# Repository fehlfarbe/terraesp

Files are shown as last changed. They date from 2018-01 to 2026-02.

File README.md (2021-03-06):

# ESP32 terrarium controller

With this project you can control your terrarium's temperature, light, sprinkler and so on via webinterface.

## Features

* Reads different Sensors for temperature and humidity (DHT22, SHT3x, DS1820, ...) and analog sensors to measure soil moisture etc.
* Timers for day/night light switch
* Actions if threshold for a sensor is reached e.g. to start sprinkler for 10s if humidity is under threshold
* Webinterface:
  * 24h log of temperature and humidity, actions etc.
  * control for buttons/actors and sliders for PWM pins
  * change config
* OTA update via WiFi

## Webinterface

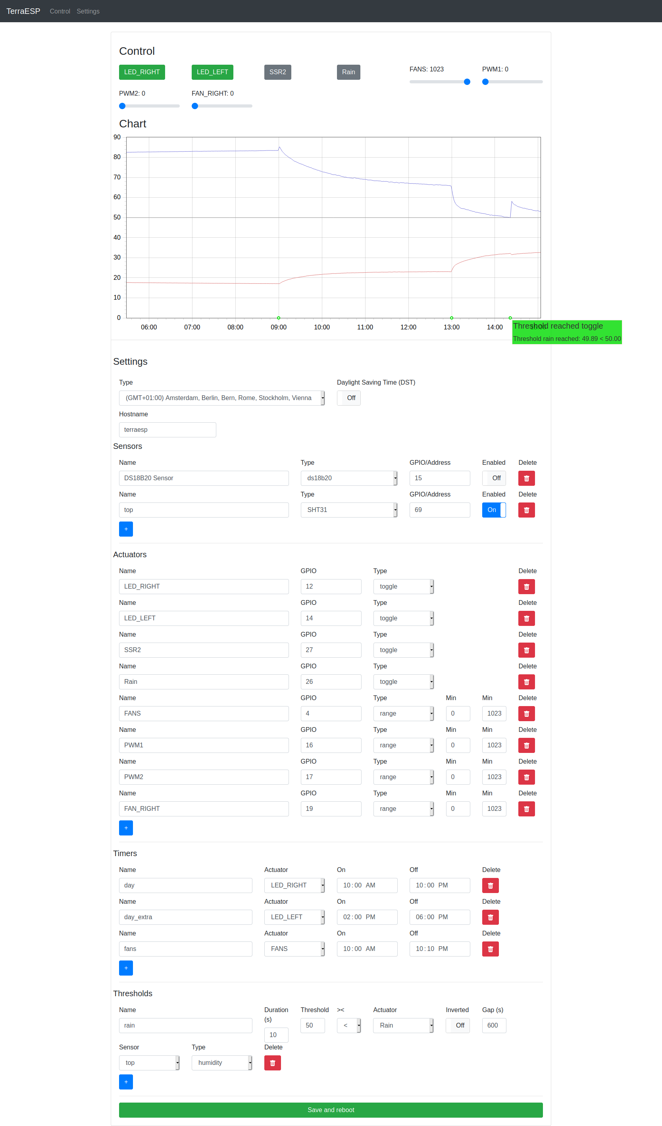
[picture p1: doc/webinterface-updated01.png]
webinterface Screenshot of webinterface


The webinterface has interactive controls to toggle relays or set PWM values to set the brightness of LEDs or fan speed.

A chart shows the measured temperatures (red) and humidity (blue) of your configured sensors and events (green) like time on, off and so on.

You can add sensors, actuators (relay, pwm), timers and thresholds in the 'settings' section.

## Parts needed

* ESP32 dev board
* DHT22 / SHT31 / analog temperature and humidity sensor
* Relay or SSR board to control lights/pump
* MOSFET board to control LED brightness, fan speed etc. via PWM
* WiFi connection for time sync

The device creates an access point on first start. Then you can configure your WiFi and pin settings.

## Caution

The WiFi password is saved without encryption on the device. Also OTA-update has default password "admin" at the moment. Change it if you want to secure your device for unauthorized updates.

> **Make the webinterface accessible from the internet is a very bad idea! Please use a VPN or something else to prevent a flooded terrarium ;-)**

## Installation

* Download / Clone this repository
* Install PlatformIO: <https://docs.platformio.org/en/latest/ide/pioide.html>
* Open this project in PlatformIO
* Connect your ESP32 via USB cable and upload sketch and [filesystem](https://docs.platformio.org/en/latest/platforms/espressif32.html#uploading-files-to-file-system-spiffs)
  * Run task -> Upload file system image
  * or run `pio run -t uploadfs`
  * Uploading filesystem will overwrite your settings!
* Reboot ESP32, it will create an AccessPoint with name ESP_xxxx
* Connect to the AP and open <http://192.168.4.1> in Browser
* Connect to your WiFi network
* Setup pins, sensor and so on in the webinterface

## Problems

* If PlatformIO can't find the libraries, switch to the cloned directory, open a terminal and type `pio lib install`. The command should download all necessary libraries.
* Windows users: if you get errors like `error: 'timeinfo' has incomplete type` just delete the `Time.h` header in `.pio/libdeps/{ota,usb}/Time` after installing the libs. The bug happens only on Windows because it's not case-sensitive and mixes the `time.h` header with `Time.h` of TimeLib library.

## PCB

Prototype PCB with several new features:

* 12V supply voltage for board and PWM/switches
* Directly soldered ESP32 with 12V -> 5V -> 3V3 converter
* 4x SSR to switch 230V AC with one 230V AC input and 3-4x outputs (is this safe??)
* 4x MOSFETs for PWM with supply voltage (to set the brightness of a 12V LED strip or control the speed of a fan)
* Connect multiple sensors/displays/whatever via i2c bus
* Connect analog sensors

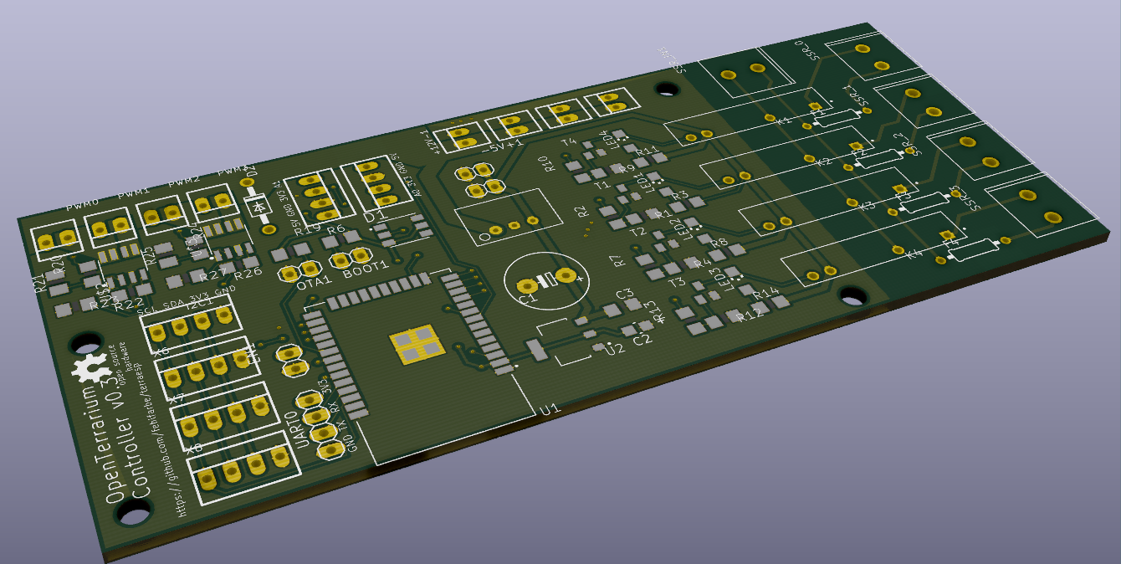
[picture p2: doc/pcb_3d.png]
PCB


## ToDo

* [ ] webinterface with authorization
* [ ] better instructions
* [ ] import/export config
* [x] The current hardware setup is a mess  with many jumper cables and so on. So I want to create PCB with relays/SSR, MOSFETS, power supply
* [ ] PID controller for heater/humidifier?
* [ ] PCB: switch from EAGLE to KiCAD (in progress...)
* [ ] PCB: replace the expensive 12V -> 5V step down (in progress...)

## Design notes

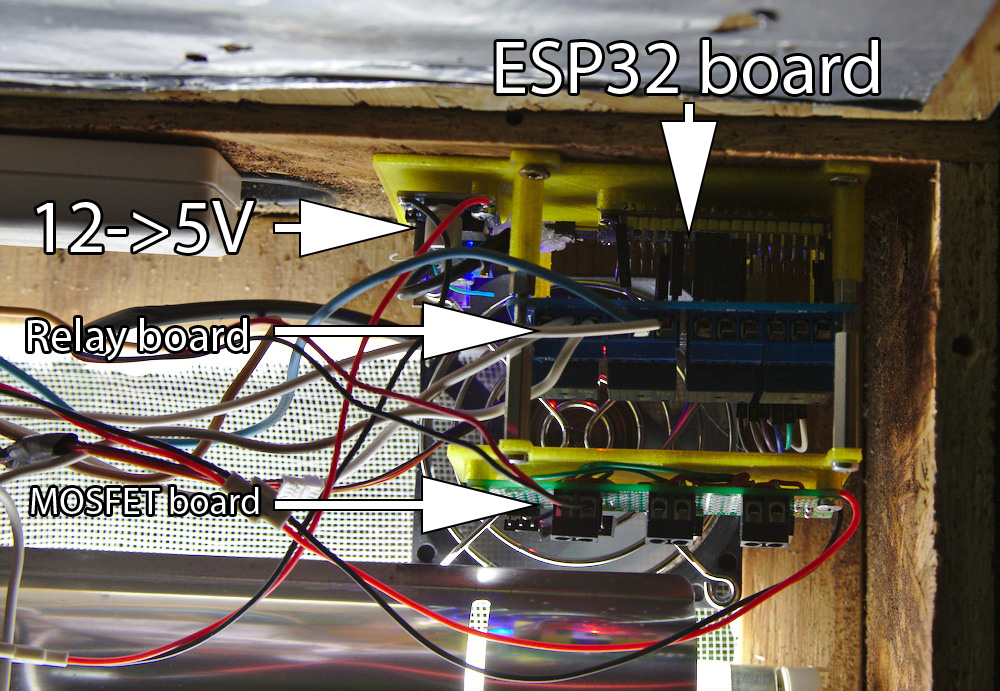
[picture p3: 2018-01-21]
doc/terrarium03.jpg

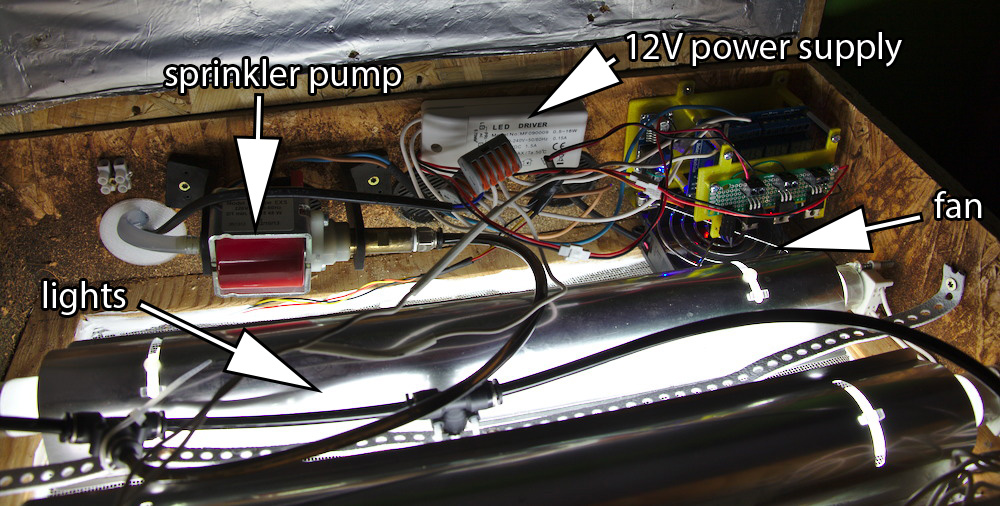
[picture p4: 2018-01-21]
doc/terrarium02.jpg

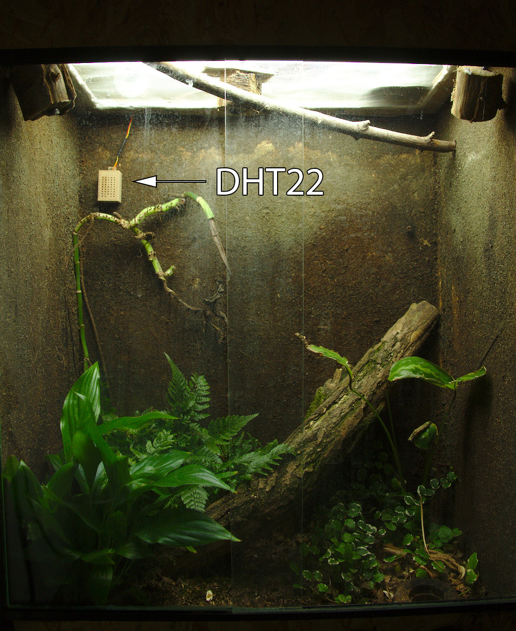
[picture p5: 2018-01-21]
doc/terrarium01.jpg

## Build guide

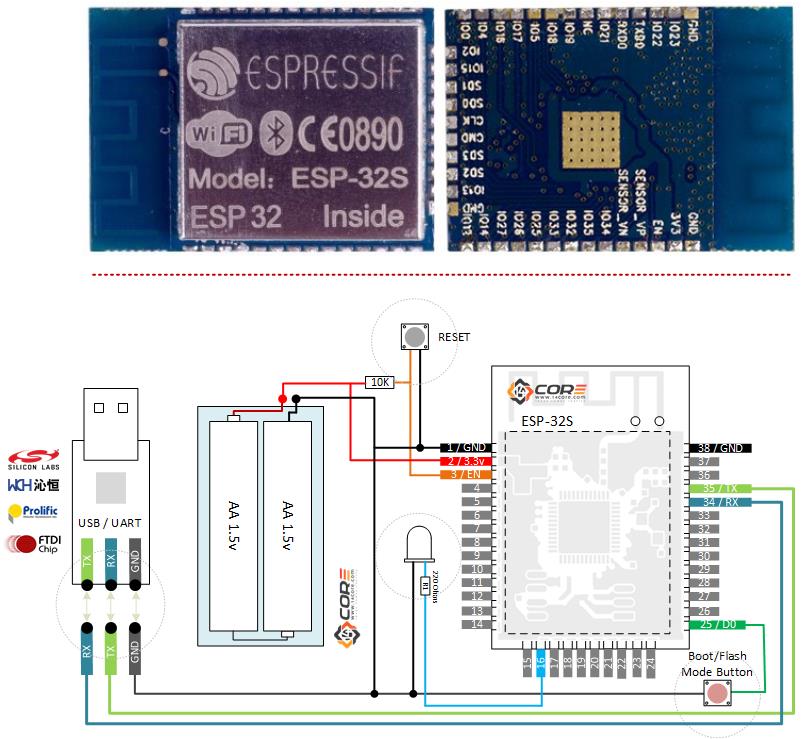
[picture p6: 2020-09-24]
doc/ESP32-Flash-USB-UART-Wiring-Guide-diagram.jpg

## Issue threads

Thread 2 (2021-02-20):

multiple time errors when compiling

jonathoncain, 2021-02-20:
I'm getting multiple time errors when compiling. specifically to deal with time.
[errors.txt](https://github.com/fehlfarbe/terraesp/files/6014123/errors.txt)

fehlfarbe, 2021-02-20:
Hi!
Did you try the master branch? I updated many things in [version2](https://github.com/fehlfarbe/terraesp/tree/version2 ) branch.

jonathoncain, 2021-02-20:
Yes I tried it first and was getting errors when compiling as well. I can
send the errors from that as well when I get home. It was right at the
beginning of the compiling. It was dealing with the feature/stage said it
wasnt in the upper stream or something like that.

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

jonathoncain, 2021-02-20:
I wanted to clarify my earlier response. Version2 is the one I was having the errors on. I uploaded a copy of the terminal output.

fehlfarbe, 2021-02-21:
Could be related to this problem: https://community.platformio.org/t/build-error-if-time-library-is-installed/450/6

I'm working on Linux so I can't really test it but I fixed some includes and I hope it will compile now.

jonathoncain, 2021-02-21:
its still failing with fewer errors.
[errors2.txt](https://github.com/fehlfarbe/terraesp/files/6017058/errors2.txt)

fehlfarbe, 2021-02-23:
I updated some imports and added a note for Windows users:

> Windows users: if you get errors like `error: 'timeinfo' has incomplete type` just delete the `Time.h` header in `.pio/libdeps/{ota,usb}/Time`. The bug happens only on Windows because it's not case-sensitive and mixes the `time.h` header with `Time.h` of TimeLib library.

It's a problem of the TimeLib dependency and the `Time.h` header will be removed in the future. After deleting `Time.h` it compiles on Windows.

jonathoncain, 2021-02-26:
The code is compiling without issue now. However it will not upload it says to specify upload port which I tried to add to the .ini file and have had no luck. It's like it doesn't recognize the board. If I create a new project and select the doit board version it uploads the blink sketch just fine so I don't know what the issue is

fehlfarbe, 2021-03-04:
Hey sorry for my late response. Did you select the USB environment in platformio?

You can also delete the OTA environment if you don't use OTA.:
```
[env:ota]
build_flags = -D RELEASE
upload_protocol = espota
upload_port = terraesp.local
upload_flags =
    --auth=admin
```

jonathoncain, 2021-03-06:
i figured it out it compiles and uploads. but when using the pio run -t uploadfs i get and error in the terminal windows that opens. i have attached the errors.
[error.txt](https://github.com/fehlfarbe/terraesp/files/6094764/error.txt)

fehlfarbe, 2021-03-06:
I added `mklittlefs.exe` to the project that should enable LittleFS build for Windows. Please pull and try again :)

jonathoncain, 2021-03-07:
thank you for all the help. its working now

fehlfarbe, 2021-03-07:
You're welcome! Feel free to open a new issue if you need more help.

Closed 2021-03-07.

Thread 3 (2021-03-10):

temp sensor not working

jonathoncain, 2021-03-10:
I have gotten it working and have it connected to the WIFI but I'm experiencing two issues.  the temp sensor isnt working i have tried a dht11 and dht22 (I noticed there isn't an option for the dht22 but i tried it on the 11 setting). I was using the pull-up resistor with the sensors. the other isue is its not geting the time from the internet it always starts at 00:00 when i connect it.

fehlfarbe, 2021-03-27:
Hey sorry for long response time. I have too much work at the moment.
I switched back to Adafruit DHT library and tried with AM2301 sensor which was working.

Time problem: can you ping `0.de.pool.ntp.org` and `1.de.pool.ntp.org` that's the NTP servers I'm using for time sync at the moment. Maybe I should add an option to set time via browser interface.

jonathoncain, 2021-03-29:
I'm not sure what is happening but once I upload the new version2 the esp never turns on the access point for me to connect to my home Wi-Fi. I uploaded the old version and it works so I'm assuming something is broken since the update. I also had a question is the master still different than version2 or are they the same now. should I just be using the master or version2. I have been using the master to upload the filesystem because it still fails on version2 then I switch to version to to upload the code.

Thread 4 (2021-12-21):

Problem Compiling

TomBoundless, 2021-12-21:
Sorry if this is not the correct place to post this, but I'm having issues around the DHT sensor.

In file included from src/sensors/dht_sensor.cpp:1:0:
src/sensors/dht_sensor.h:24:9: error: 'DHT' does not name a type
         DHT *sensor = nullptr;
         ^
src/sensors/dht_sensor.cpp: In constructor 'DHT11Sensor::DHT11Sensor(String, uint8_t, uint8_t)':
src/sensors/dht_sensor.cpp:7:5: error: 'sensor' was not declared in this scope
     sensor = new DHT(pin, type);
     ^
src/sensors/dht_sensor.cpp:7:18: error: expected type-specifier before 'DHT'
     sensor = new DHT(pin, type);
                  ^
src/sensors/dht_sensor.cpp: In member function 'bool DHT11Sensor::updateValues()':
src/sensors/dht_sensor.cpp:34:21: error: 'sensor' was not declared in this scope
     m_temperature = sensor->readTemperature();
                     ^
src/sensors/dht_sensor.cpp:95:1: warning: no return statement in function returning non-void [-Wreturn-type]
 }
 ^
*** [.pio\build\usb\src\sensors\dht_sensor.cpp.o] Error 1

I can't seem to figure out what the problem is. Running on platformio in VS Code.

fehlfarbe, 2021-12-21:
Does it work when you open a terminal in VSCode and install the libraries with `pio lib install`?

TomBoundless, 2021-12-21:
It doesn't unfortunately.

The annoying thing is I'm not even using the DHT sensor, planning on using an SHT

fehlfarbe, 2021-12-21:
Quick fix: I removed the include of dht_sensor in terrasesp.cpp and created a new branch: https://github.com/fehlfarbe/terraesp/tree/no-dht can you try it?

TomBoundless, 2021-12-21:
Thanks for your quick responses.

It's giving me the same error again.

fehlfarbe, 2021-12-21:
Maybe I found the initial bug: are you using Windows? There is a different/old `dht.h` in the `src` directory. Maybe Windows includes the old `dht.h` in `src` directory instead of the Adafruit `DHT.h` because it's case-insensitive. I removed the old `dht.h` in my latest commit on master branch.

TomBoundless, 2021-12-21:
I am using Windows.

That latest commit has solved the problem and it has now successfully compiled!

Thanks very much for your help, this will make a brilliant Christmas present for my girlfriend.

fehlfarbe, 2021-12-21:
Perfect! :smiley:
Just open a new issue if something else doesn't work.

TomBoundless, 2021-12-21:
Thanks very much!

Closed 2021-12-21.

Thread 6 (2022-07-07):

Compiling error

Eisbaeeer, 2022-07-07:
Platformio get an error by compiling the code.
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

src/Threshold.cpp:132:43: error: call of overloaded 'abs(long unsigned int)' is ambiguous

LuigiPapparotti, 2023-07-29:
Cast the argument to **abs()** to **int** or another suitable type:

`if(is_active && abs(((int)millis()-activated))/1000.0 > duration){`

Closed 2023-10-19.

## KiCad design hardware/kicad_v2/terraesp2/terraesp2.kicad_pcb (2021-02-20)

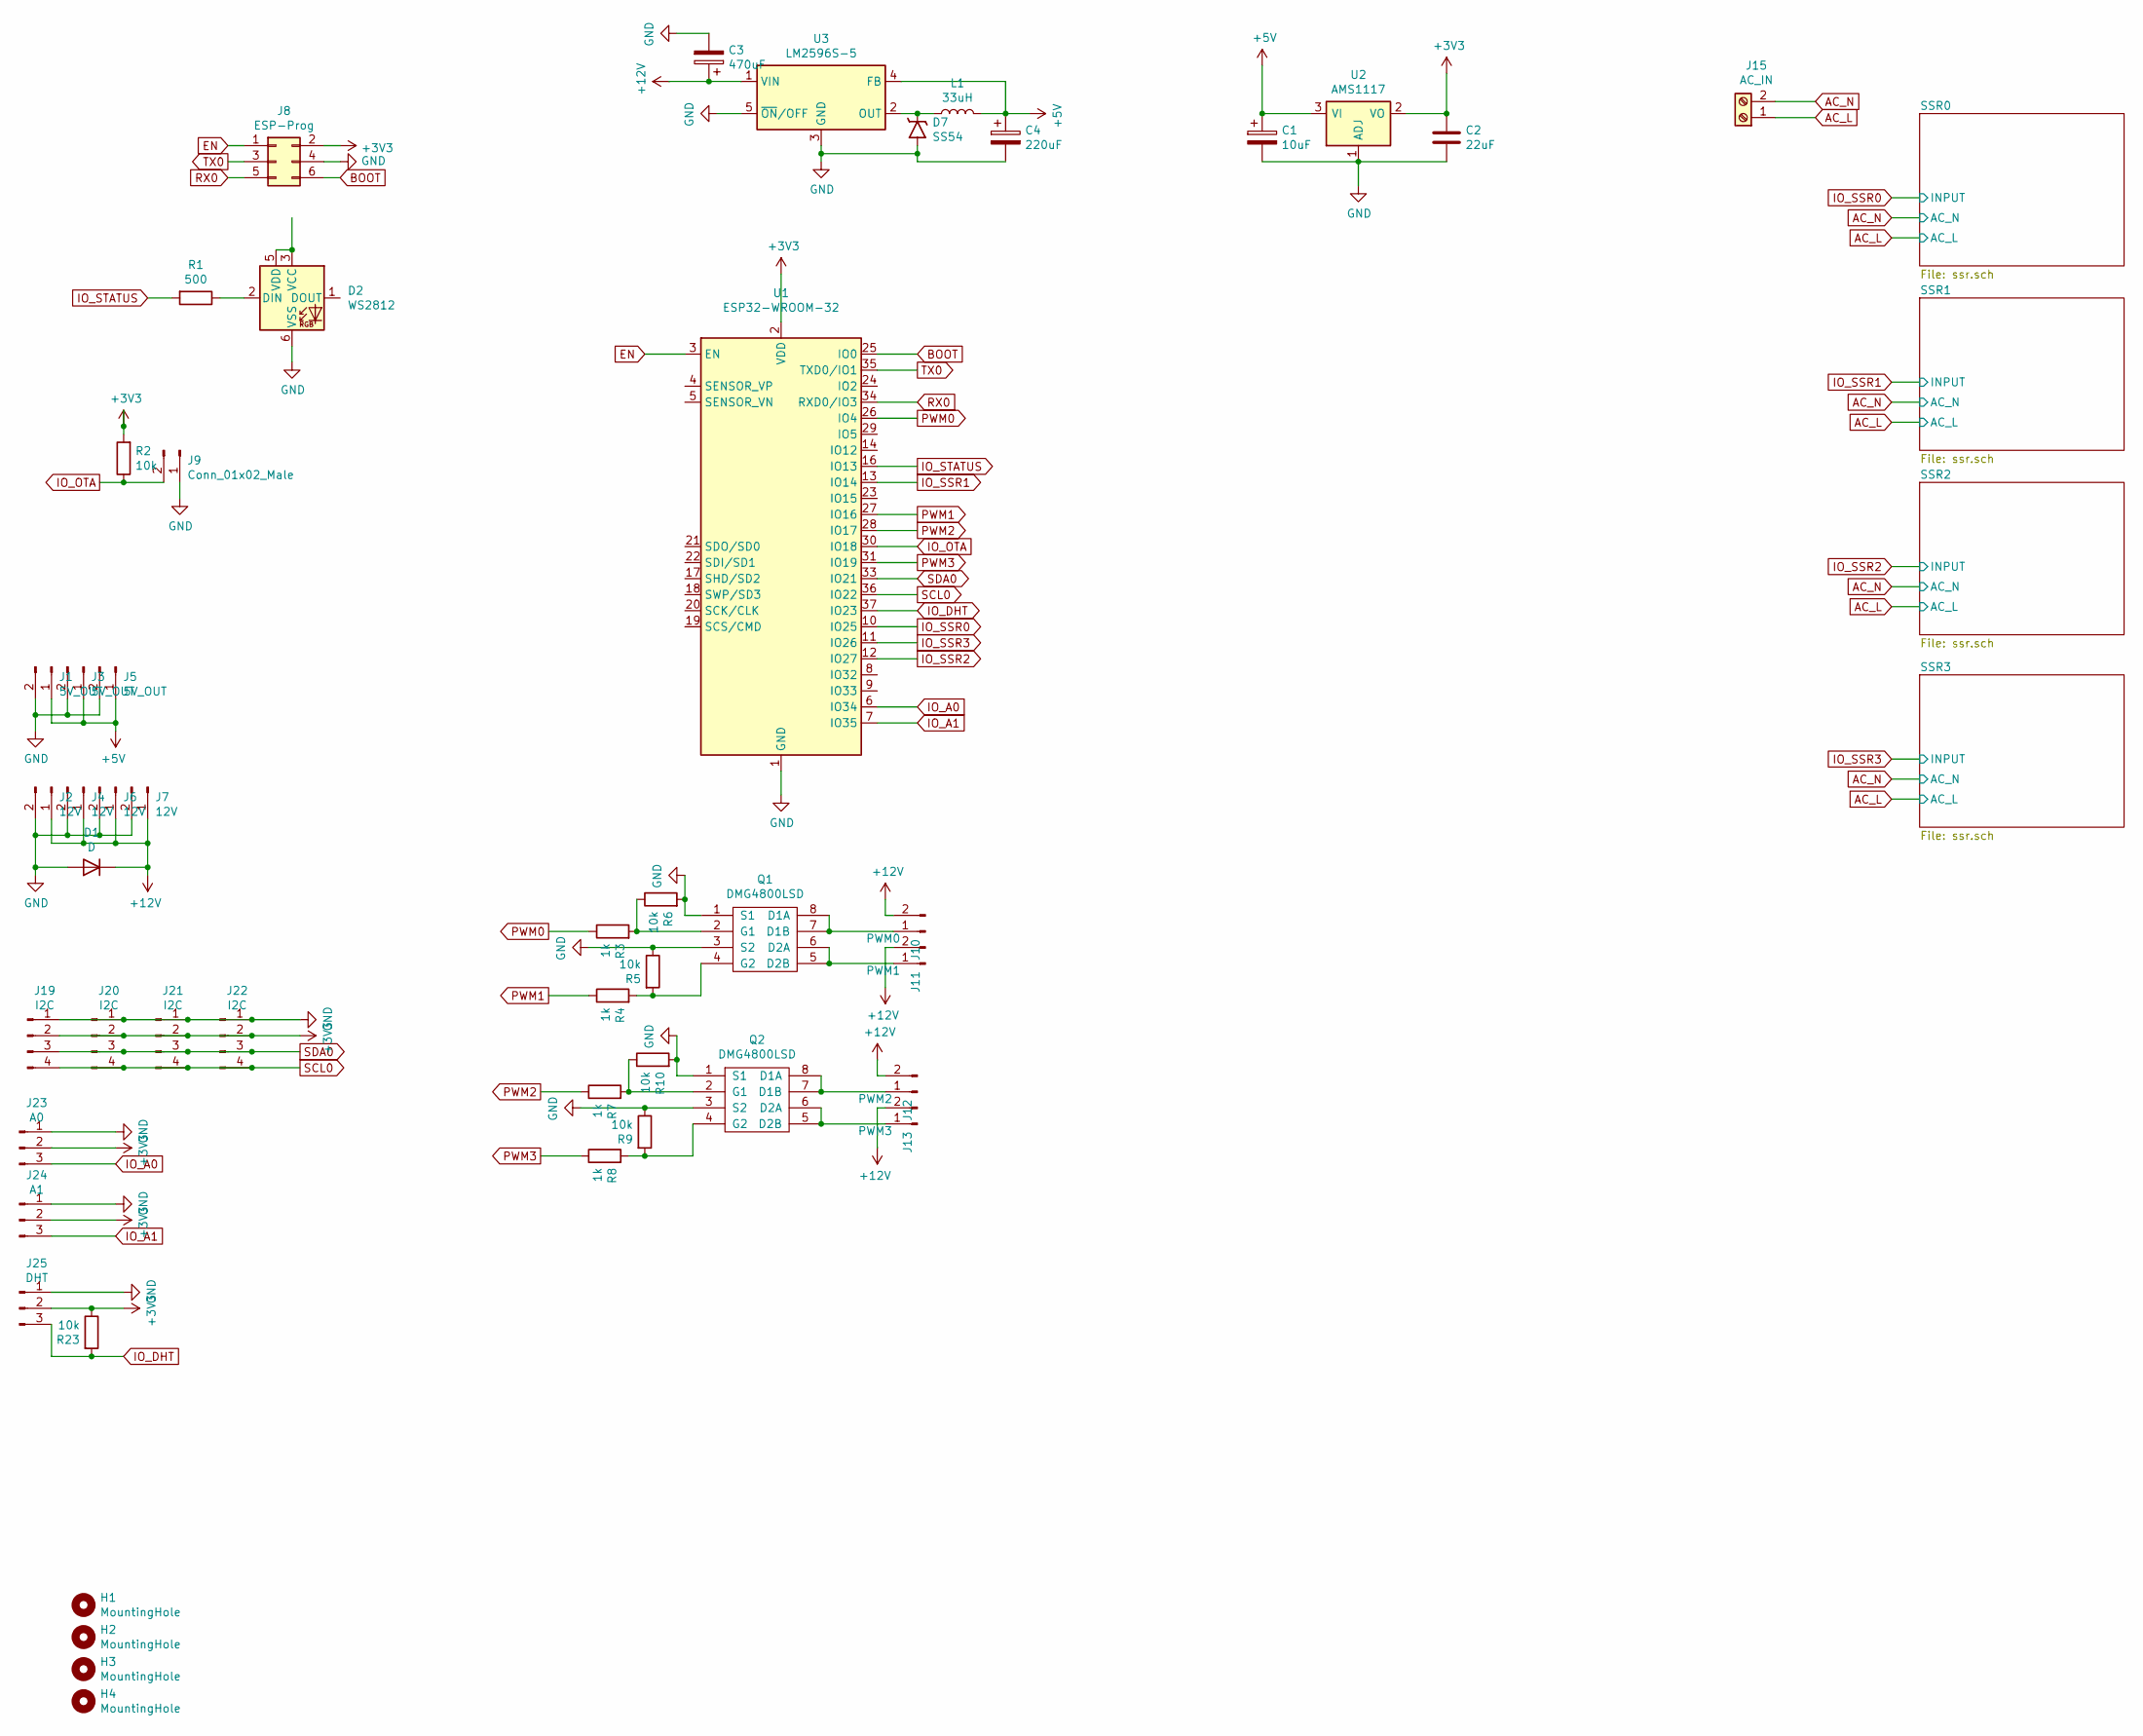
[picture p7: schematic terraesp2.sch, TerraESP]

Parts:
C1: 10uF; C_1206_3216Metric
C2: 22uF; CP_EIA-1608-08_AVX-J
C3: 470uF; CP_Elec_10x10.5
C4: 220uF; CP_Elec_6.3x5.8
D1: D; D_1206_3216Metric
D2: WS2812; LED_WS2812_PLCC6_5.0x5.0mm_P1.6mm
D7: SS54; DO-214AC
H1, H2, H3, H4: MountingHole; MountingHole_3.2mm_M3
J1, J3, J5: 5V_OUT; Molex_KK-254_AE-6410-02A_1x02_P2.54mm_Vertical
J2, J4, J6, J7: 12V; Molex_KK-254_AE-6410-02A_1x02_P2.54mm_Vertical
J8: ESP-Prog; IDC-Header_2x03_P2.54mm_Vertical
J9: Conn_01x02_Male; PinHeader_1x02_P2.54mm_Vertical
J10: PWM0; Molex_KK-254_AE-6410-02A_1x02_P2.54mm_Vertical
J11: PWM1; Molex_KK-254_AE-6410-02A_1x02_P2.54mm_Vertical
J12: PWM2; Molex_KK-254_AE-6410-02A_1x02_P2.54mm_Vertical
J13: PWM3; Molex_KK-254_AE-6410-02A_1x02_P2.54mm_Vertical
J15: AC_IN; TerminalBlock_Phoenix_MKDS-1,5-2_1x02_P5.00mm_Horizontal
J19, J20, J21, J22: I2C; Molex_KK-254_AE-6410-04A_1x04_P2.54mm_Vertical
J23: A0; Molex_KK-254_AE-6410-03A_1x03_P2.54mm_Vertical
J24: A1; Molex_KK-254_AE-6410-03A_1x03_P2.54mm_Vertical
J25: DHT; Molex_KK-254_AE-6410-03A_1x03_P2.54mm_Vertical
L1: 33uH; L_12x12mm_H8mm
Q1, Q2: DMG4800LSD; Diodes_Inc.-SO-8-03_2017-0-MFG
R1: 500; R_1206_3216Metric
R2, R5, R6, R9, R10, R23: 10k; R_1206_3216Metric
R3, R4, R7, R8: 1k; R_1206_3216Metric
U1: ESP32-WROOM-32
U2: AMS1117; SOT-223-3_TabPin2
U3: LM2596S-5; TO-263-5_TabPin3

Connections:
+3V3: C2.1, J8.2, J19.2, J20.2, J21.2, J22.2, J23.2, J24.2, J25.2, R2.2, R23.1, U1.2 (VDD), U2.2 (VO)
+5V: C1.1, C4.1, J1.1, J3.1, J5.1, L1.2, U2.3 (VI), U3.4 (FB); also elsewhere on the board
+12V: C3.1, D1.1 (K), J2.1, J4.1, J6.1, J7.1, J10.2, J11.2, J12.2, J13.2, U3.1 (VIN)
AC_L: J15.1; also elsewhere on the board
AC_N: J15.2; also elsewhere on the board
BOOT: J8.6, U1.25 (IO0)
EN: J8.1, U1.3 (EN)
GND: C1.2, C2.2, C3.2, C4.2, D1.2 (A), D2.6 (VSS), D7.A, J1.2, J2.2, J3.2, J4.2, J5.2, J6.2, J7.2, J8.4, J9.1, J19.1, J20.1, J21.1, J22.1, J23.1, J24.1, J25.1, Q1.1 (S1), Q1.3 (S2), Q2.1 (S1), Q2.3 (S2), R5.1, R6.2, R9.1, R10.2, U1.1 (GND), U1.15 (GND), U1.38 (GND), U1.39 (GND), U2.1 (ADJ), U3.3 (GND), U3.5 (~ON~/OFF); also elsewhere on the board
IO_A0: J23.3, U1.6 (IO34)
IO_A1: J24.3, U1.7 (IO35)
IO_DHT: J25.3, R23.2, U1.37 (IO23)
IO_OTA: J9.2, R2.1, U1.30 (IO18)
IO_SSR0: U1.10 (IO25); also elsewhere on the board
IO_SSR1: U1.13 (IO14); also elsewhere on the board
IO_SSR2: U1.12 (IO27); also elsewhere on the board
IO_SSR3: U1.11 (IO26); also elsewhere on the board
IO_STATUS: R1.2, U1.16 (IO13)
unnamed: D2.2 (DIN), R1.1
unnamed: D2.3 (VCC), D2.5 (VDD)
unnamed: D7.C, L1.1, U3.2 (OUT)
unnamed: J10.1, Q1.7 (D1B), Q1.8 (D1A)
unnamed: J11.1, Q1.5 (D2B), Q1.6 (D2A)
unnamed: J12.1, Q2.7 (D1B), Q2.8 (D1A)
unnamed: J13.1, Q2.5 (D2B), Q2.6 (D2A)
unnamed: Q1.2 (G1), R3.2, R6.1
unnamed: Q1.4 (G2), R4.2, R5.2
unnamed: Q2.2 (G1), R7.2, R10.1
unnamed: Q2.4 (G2), R8.2, R9.2
PWM0: R3.1, U1.26 (IO4)
PWM1: R4.1, U1.27 (IO16)
PWM2: R7.1, U1.28 (IO17)
PWM3: R8.1, U1.31 (IO19)
RX0: J8.5, U1.34 (RXD0/IO3)
SCL0: J19.4, J20.4, J21.4, J22.4, U1.36 (IO22)
SDA0: J19.3, J20.3, J21.3, J22.3, U1.33 (IO21)
TX0: J8.3, U1.35 (TXD0/IO1)

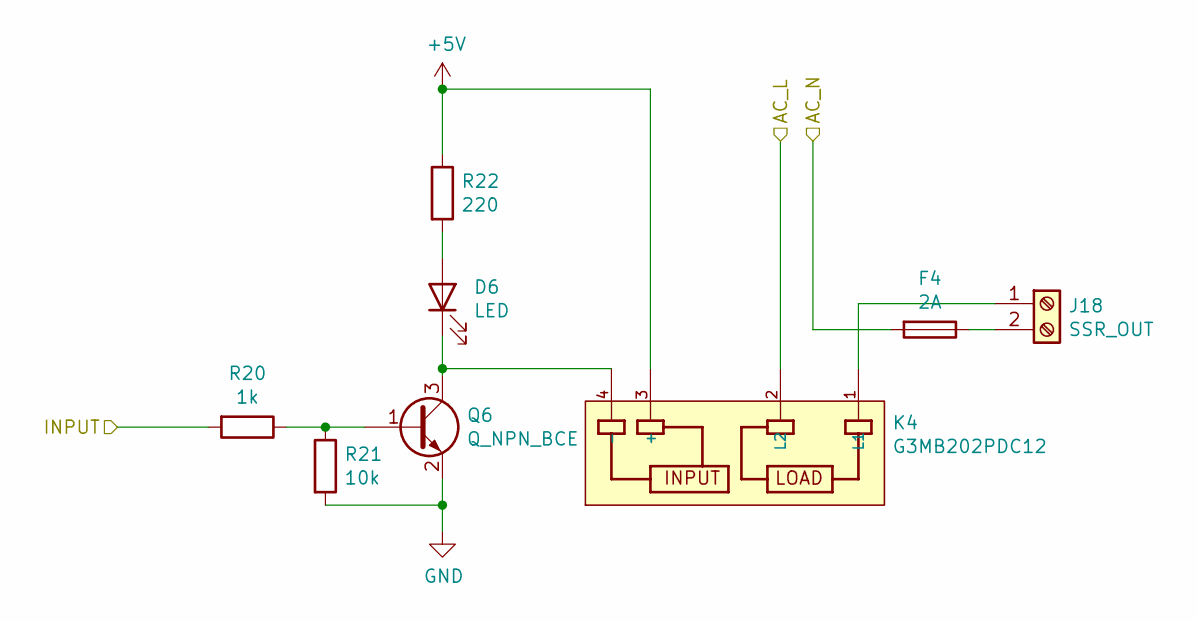
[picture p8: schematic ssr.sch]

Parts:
D3: LED; LED_1206_3216Metric
F1: 2A; ASI PTF-76 5x20mm Fuse Holder
J14: SSR_OUT; TerminalBlock_Phoenix_MKDS-1,5-2_1x02_P5.00mm_Horizontal
K1: G3MB202PDC12; RELAY_G3MB202PDC12; PARTREV N/A
Q3: Q_NPN_BCE; SOT-23
R11: 1k; R_1206_3216Metric
R12: 10k; R_1206_3216Metric
R13: 220; R_1206_3216Metric

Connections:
+5V: K1.3 (+), R13.1; also elsewhere on the board
AC_L: K1.2 (L2); also elsewhere on the board
AC_N: F1.2; also elsewhere on the board
GND: Q3.2 (E), R12.2; also elsewhere on the board
IO_SSR0: R11.2; also elsewhere on the board
unnamed: D3.1 (K), K1.4 (-), Q3.3 (C)
unnamed: D3.2 (A), R13.2
unnamed: F1.1, J14.2
unnamed: J14.1, K1.1 (L1)
unnamed: Q3.1 (B), R11.1, R12.1

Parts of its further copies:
D4, D5, D6: LED; LED_1206_3216Metric
F2, F3, F4: 2A; ASI PTF-76 5x20mm Fuse Holder
J16, J17, J18: SSR_OUT; TerminalBlock_Phoenix_MKDS-1,5-2_1x02_P5.00mm_Horizontal
K2, K3, K4: G3MB202PDC12; RELAY_G3MB202PDC12; PARTREV N/A
Q4, Q5, Q6: Q_NPN_BCE; SOT-23
R14, R17, R20: 1k; R_1206_3216Metric
R15, R18, R21: 10k; R_1206_3216Metric
R16, R19, R22: 220; R_1206_3216Metric

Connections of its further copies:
+5V: K2.3 (+), K3.3 (+), K4.3 (+), R16.1, R19.1, R22.1; also elsewhere on the board
AC_L: K2.2 (L2), K3.2 (L2), K4.2 (L2); also elsewhere on the board
AC_N: F2.2, F3.2, F4.2; also elsewhere on the board
GND: Q4.2 (E), Q5.2 (E), Q6.2 (E), R15.2, R18.2, R21.2; also elsewhere on the board
IO_SSR1: R14.2; also elsewhere on the board
IO_SSR2: R17.2; also elsewhere on the board
IO_SSR3: R20.2; also elsewhere on the board
unnamed: D4.1 (K), K2.4 (-), Q4.3 (C)
unnamed: D4.2 (A), R16.2
unnamed: D5.1 (K), K3.4 (-), Q5.3 (C)
unnamed: D5.2 (A), R19.2
unnamed: D6.1 (K), K4.4 (-), Q6.3 (C)
unnamed: D6.2 (A), R22.2
unnamed: F2.1, J16.2
unnamed: F3.1, J17.2
unnamed: F4.1, J18.2
unnamed: J16.1, K2.1 (L1)
unnamed: J17.1, K3.1 (L1)
unnamed: J18.1, K4.1 (L1)
unnamed: Q4.1 (B), R14.1, R15.1
unnamed: Q5.1 (B), R17.1, R18.1
unnamed: Q6.1 (B), R20.1, R21.1

Board: 2 copper layers, 81 parts (0 on the bottom side), 56 nets, no tracks yet.

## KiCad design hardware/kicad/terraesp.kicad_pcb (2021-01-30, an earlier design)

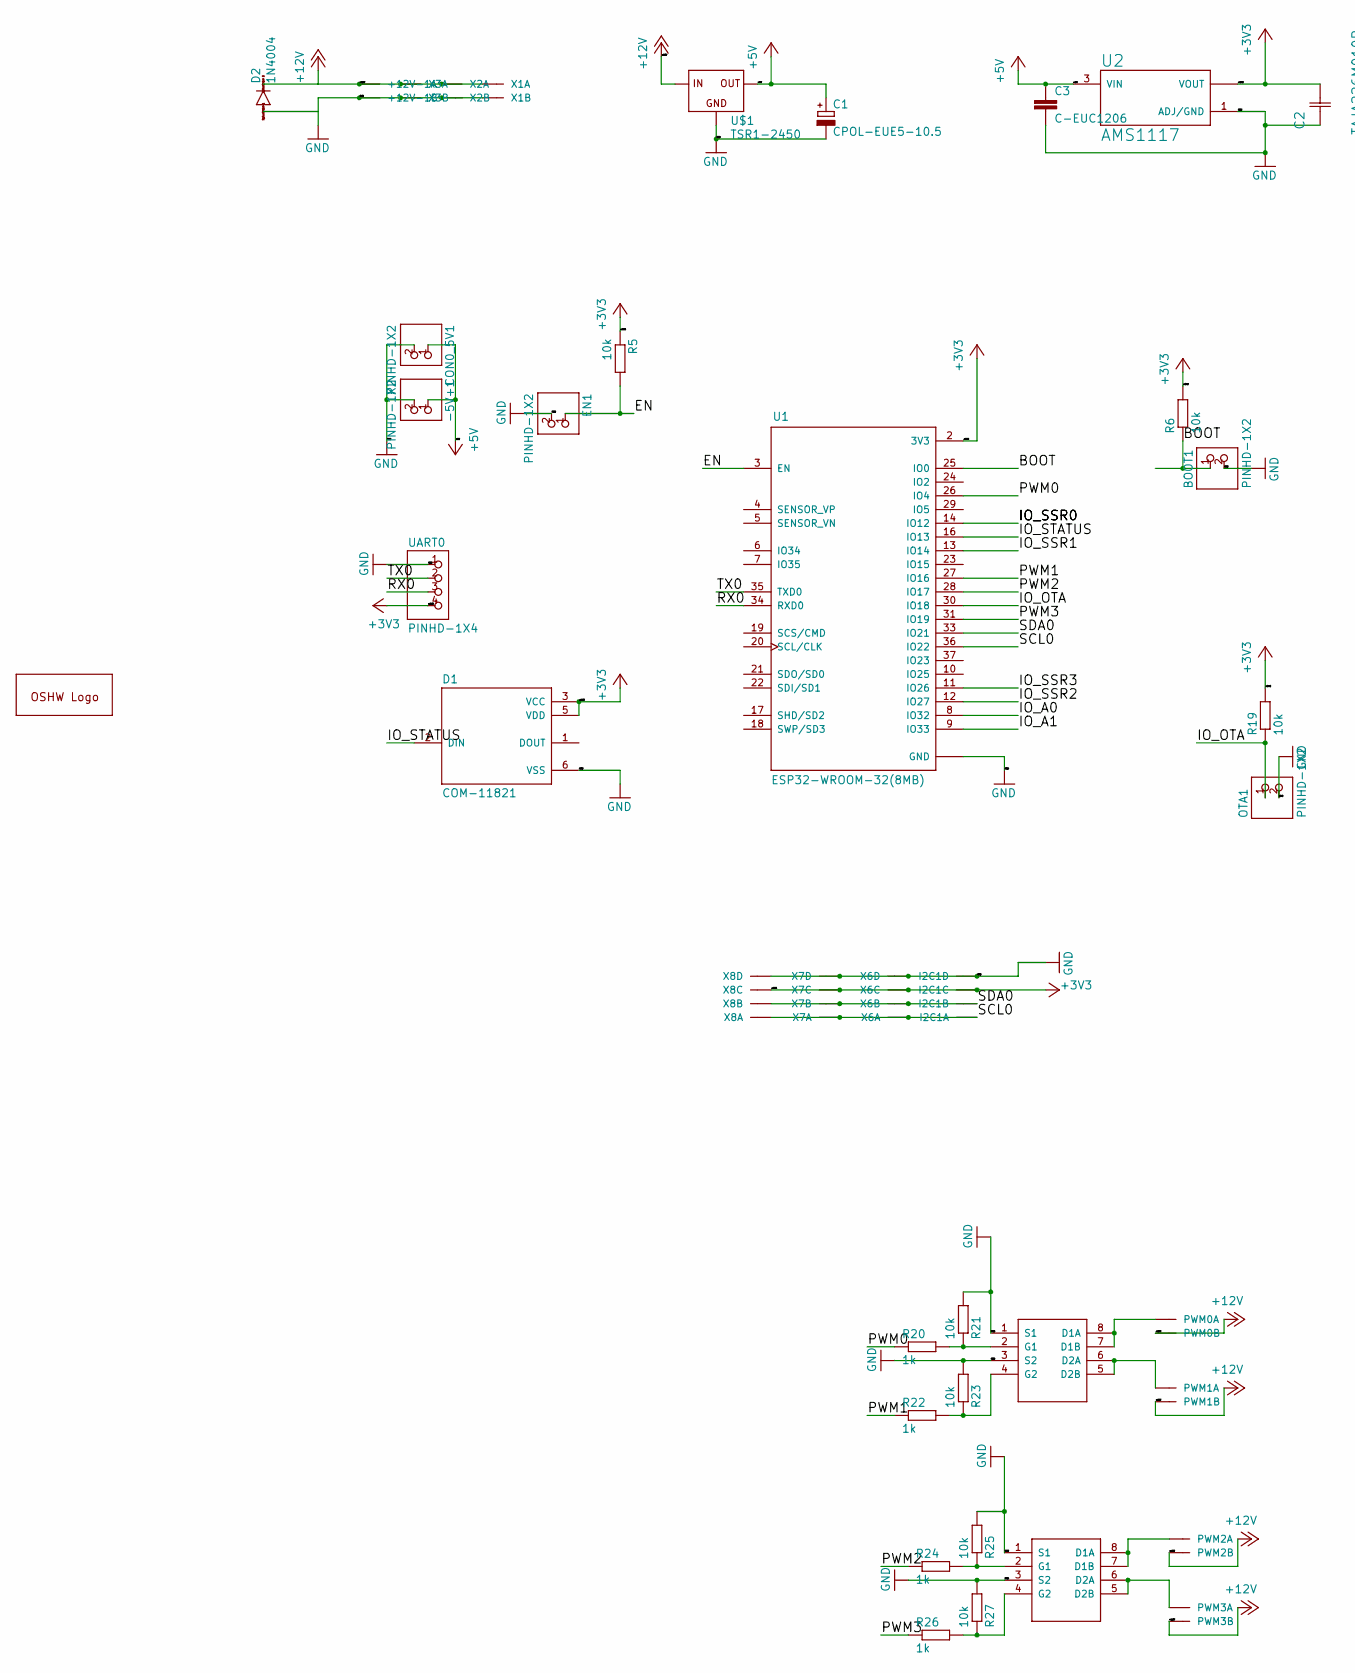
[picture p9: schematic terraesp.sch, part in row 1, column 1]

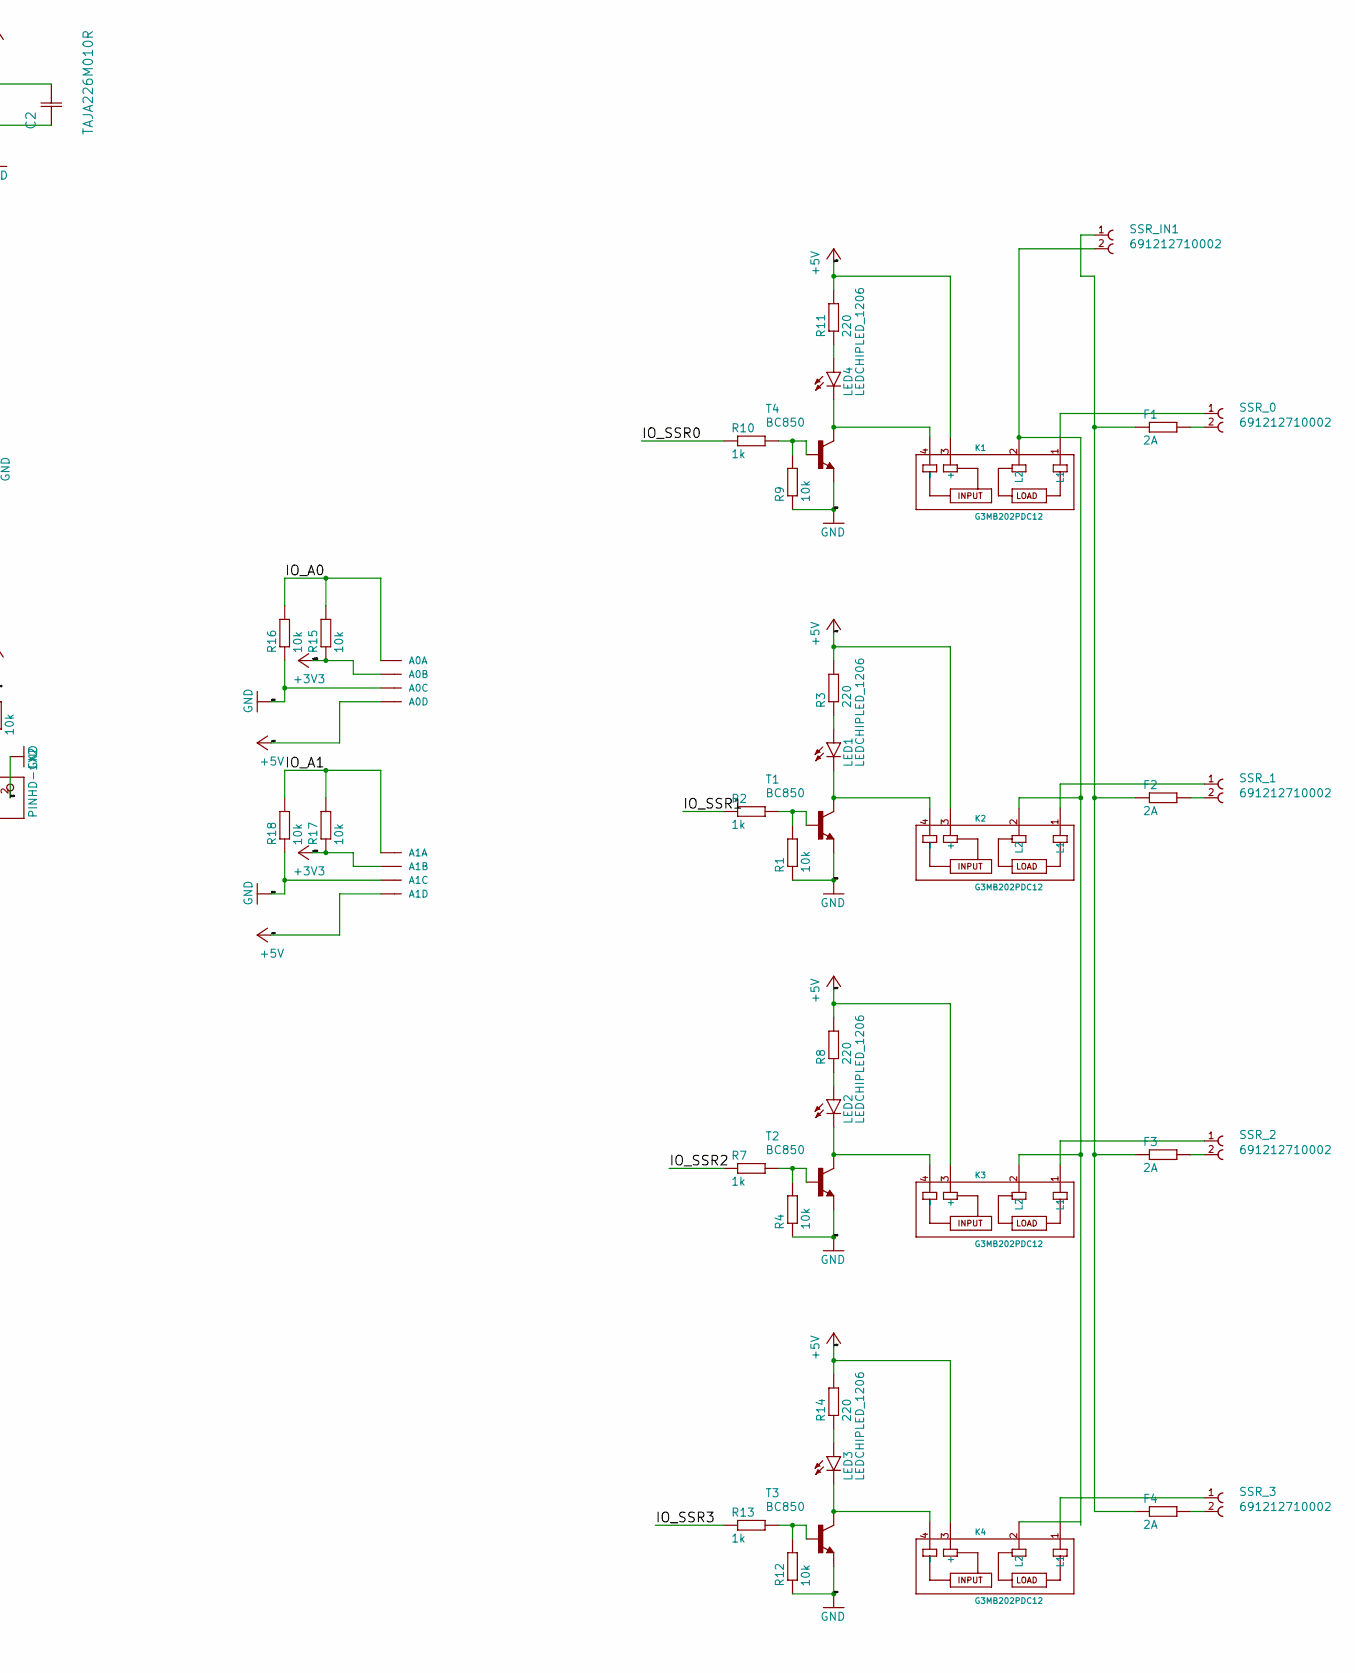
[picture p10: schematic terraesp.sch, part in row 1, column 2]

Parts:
+12V-1: 22-23-2021
-5V+1: PINHD-1X2; 1X02
A0, A1: 22-23-2041
BOOT1: PINHD-1X2; 1X02
C1: CPOL-EUE5-10.5; E5-10,5
C2: TAJA226M010R; CAPCP3216X180N
C3: C-EUC1206; C1206
CON0_5V1: PINHD-1X2; 1X02
D1: COM-11821; LED_COM-11821
D2: 1N4004; DO41-10
EN1: PINHD-1X2; 1X02
F1, F2, F3, F4: 2A; 0207_10
GOLD_ORB_SM2: OSHWLOGOLOGO5MM; OSHW_5MM
I2C1: 22-23-2041
K1, K2, K3, K4: G3MB202PDC12; RELAY_G3MB202PDC12
LED1, LED2, LED3, LED4: LEDCHIPLED_1206; CHIPLED_1206
OTA1: PINHD-1X2; 1X02
PWM0, PWM1, PWM2, PWM3: 22-23-2021
R1, R4, R9, R12: 10k; R1206
R2, R7, R10, R13, R20, R22, R24, R26: 1k; R1206
R3, R8, R11, R14: 220; R1206
R5, R6, R15, R16, R17, R18, R19, R21, R23, R25, R27: 10k; M1206
SSR_0, SSR_1, SSR_2, SSR_3: 691212710002
SSR_IN1: 691212710002
T1, T2, T3, T4: BC850; SOT23
U1: ESP32-WROOM-32(8MB); MODULE_ESP32-WROOM-32(8MB)
U2: AMS1117; SOT229P700X180-4N
U$1: TSR1-2450
U$2, U$3: DMG4800LSD; SOIC127P600X144-8
UART0: PINHD-1X4; 1X04
X1, X2, X3: 22-23-2021
X6, X7, X8: 22-23-2041

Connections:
+3V3: A0.2, A1.2, C2.2 (C2), D1.3 (VCC), D1.5 (VDD), I2C1.3, R5.1, R6.2, R15.1, R17.1, R19.2, U1.2 (3V3), U2.2 (VOUT), U2.4 (VOUT), UART0.4, X6.3, X7.3, X8.3
+5V: -5V+1.1, A0.4, A1.4, C1.+, C3.1, CON0_5V1.1, K1.3 (+), K2.3 (+), K3.3 (+), K4.3 (+), R3.2, R8.2, R11.2, R14.2, U2.3 (VIN), U$1.3 (OUT)
+12V: +12V-1.1, D2.C, PWM0.2, PWM1.2, PWM2.2, PWM3.2, U$1.1 (IN), X1.1, X2.1, X3.1
/BOOT: BOOT1.1, R6.1, U1.25 (IO0)
/EN: EN1.1, R5.2, U1.3 (EN)
/IO_A0: A0.1, R15.2, R16.2, U1.8 (IO32)
/IO_A1: A1.1, R17.2, R18.2, U1.9 (IO33)
/IO_OTA: OTA1.1, R19.1, U1.30 (IO18)
/IO_SSR0: R10.1, U1.14 (IO12)
/IO_SSR1: R2.1, U1.13 (IO14)
/IO_SSR2: R7.1, U1.12 (IO27)
/IO_SSR3: R13.1, U1.11 (IO26)
/IO_STATUS: D1.2 (DIN), U1.16 (IO13)
/PWM0: R20.1, U1.26 (IO4)
/PWM1: R22.1, U1.27 (IO16)
/PWM2: R24.1, U1.28 (IO17)
/PWM3: R26.1, U1.31 (IO19)
/RX0: U1.34 (RXD0), UART0.3
/SCL0: I2C1.1, U1.36 (IO22), X6.1, X7.1, X8.1
/SDA0: I2C1.2, U1.33 (IO21), X6.2, X7.2, X8.2
/TX0: U1.35 (TXD0), UART0.2
GND: +12V-1.2, -5V+1.2, A0.3, A1.3, BOOT1.2, C1.-, C2.1 (C1), C3.2, CON0_5V1.2, D1.6 (VSS), EN1.2, I2C1.4, OTA1.2, R1.1, R4.1, R9.1, R12.1, R16.1, R18.1, R21.2, R23.2, R25.2, R27.2, T1.2 (E), T2.2 (E), T3.2 (E), T4.2 (E), U1.1 (GND), U1.15 (GND), U1.38 (GND), U1.39 (GND), U2.1 (ADJ/GND), U$1.2 (GND), U$2.1 (S1), U$2.3 (S2), U$3.1 (S1), U$3.3 (S2), UART0.1, X1.2, X2.2, X3.2, X6.4, X7.4, X8.4
unnamed: F1.1, F2.1, F3.1, F4.1, SSR_IN1.1
unnamed: F1.2, SSR_0.2
unnamed: F2.2, SSR_1.2
unnamed: F3.2, SSR_2.2
unnamed: F4.2, SSR_3.2
unnamed: K1.1 (L1), SSR_0.1
unnamed: K1.2 (L2), K2.2 (L2), K3.2 (L2), K4.2 (L2), SSR_IN1.2
unnamed: K1.4 (-), LED4.C, T4.3 (C)
unnamed: K2.1 (L1), SSR_1.1
unnamed: K2.4 (-), LED1.C, T1.3 (C)
unnamed: K3.1 (L1), SSR_2.1
unnamed: K3.4 (-), LED2.C, T2.3 (C)
unnamed: K4.1 (L1), SSR_3.1
unnamed: K4.4 (-), LED3.C, T3.3 (C)
unnamed: LED1.A, R3.1
unnamed: LED2.A, R8.1
unnamed: LED3.A, R14.1
unnamed: LED4.A, R11.1
unnamed: PWM0.1, U$2.7 (D1B), U$2.8 (D1A)
unnamed: PWM1.1, U$2.5 (D2B), U$2.6 (D2A)
unnamed: PWM2.1, U$3.7 (D1B), U$3.8 (D1A)
unnamed: PWM3.1, U$3.5 (D2B), U$3.6 (D2A)
unnamed: R1.2, R2.2, T1.1 (B)
unnamed: R4.2, R7.2, T2.1 (B)
unnamed: R9.2, R10.2, T4.1 (B)
unnamed: R12.2, R13.2, T3.1 (B)
unnamed: R20.2, R21.1, U$2.2 (G1)
unnamed: R22.2, R23.1, U$2.4 (G2)
unnamed: R24.2, R25.1, U$3.2 (G1)
unnamed: R26.2, R27.1, U$3.4 (G2)

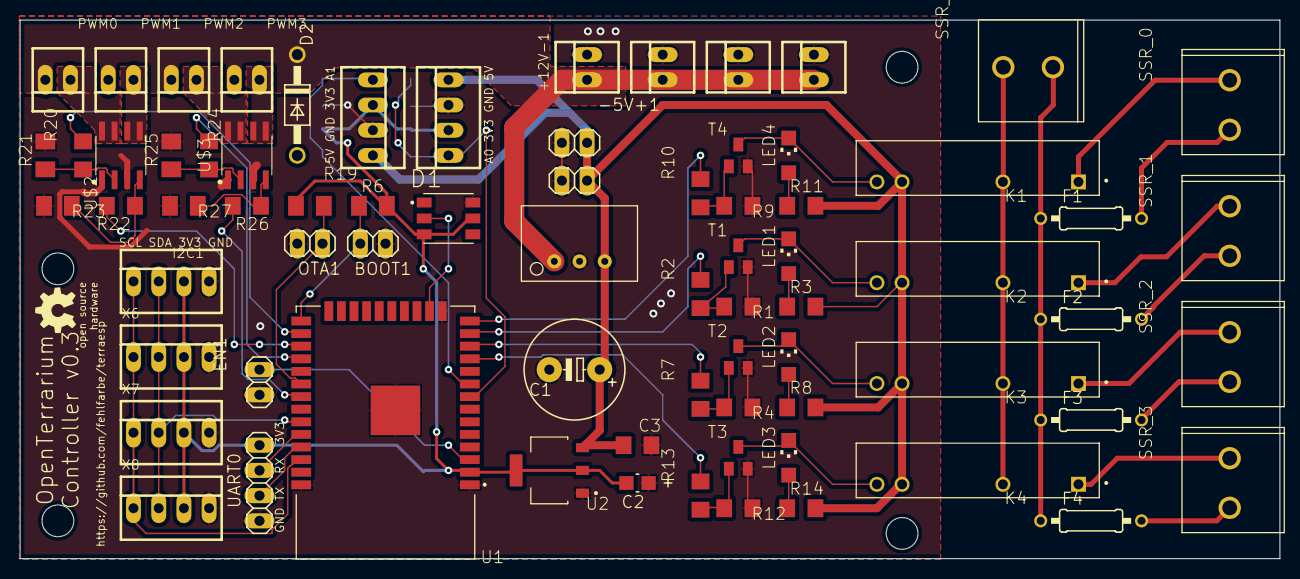
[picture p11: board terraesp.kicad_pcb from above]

Board: 2 copper layers, 127.0 x 54.3 mm, 83 parts (0 on the bottom side), 52 nets.

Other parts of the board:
@HOLE0, @HOLE1, @HOLE2, @HOLE3: (no value)

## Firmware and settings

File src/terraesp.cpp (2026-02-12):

#include <WiFi.h>
#include <ESPmDNS.h>
#include <WiFiUdp.h>
#include <ArduinoOTA.h>
#include <HTTPClient.h>
#include <ESPAsyncWebServer.h>
#include <ESPAsyncWiFiManager.h>
#include <time.h>
#include <TimeLib.h>
#include <FS.h>
#include <LittleFS.h>
#include <ArduinoJson.h>
#include <Array.h>
#include <RingBufHelpers.h>
#include <Adafruit_GFX.h>
#include <Adafruit_SSD1306.h>
#include <NeoPixelBus.h>
#include <RingBufCPP.h>
#include "Debug.h"

// #define MOCKUP_DATA
// #define LED_BUILTIN 2

// NeoPixel status
#define LED_STATUS_NEO 13

// Buffer size for 24h / 5 minutes
#define MAX_ELEMENTS 50
#define SENSORS_PAUSE_S 120

#include "sensors/sensors.h"
#include "sensors/analog_sensor.h"
#include "sensors/dht_sensor.h"
#include "sensors/sht31_sensor.h"
#include "sensors/ds18b20_sensor.h"
#include "Threshold.h"
#include "ActuatorToggle.h"
#include "ActuatorPWM.h"
#include "Timer.h"
#include "Event.h"
#include "datatypes.h"
#include "utils.h"

// status LED
// Adafruit_NeoPixel statusLED(1, LED_STATUS_NEO, NEO_GRB + NEO_KHZ800);
NeoPixelBus<NeoGrbFeature, Neo800KbpsMethod> statusLED(1, LED_STATUS_NEO);
LEDState statusLEDState = LEDState::NONE;

// WebServer
AsyncWebServer server(80);
DNSServer dns;
File fsUploadFile;

// WiFi
AsyncWiFiManager wifiManager(&server, &dns);

// settings
// String ssid = "";
// String password = "";
String host = "terraesp";
// String ap_ssid = "terraesp";
// bool ap_mode = false;
TimeSettings settings_time;
unsigned long last_sensors = 0;
Array<Threshold *, MAX_ELEMENTS> thresholds;
Array<Actuator *, MAX_ELEMENTS> actuators;
Array<Timer *, MAX_ELEMENTS> timers;
RingBufCPP<Event, 100> events;

// sensors
Array<THSensor *, MAX_ELEMENTS> sensors;
RingBufCPP<time_t, SENSORS_BUFSIZE> buffer_time;

// parallel task
TaskHandle_t pTask;

// Telnet
Debug debug;
WiFiServer telnetServer(23);
WiFiClient telnetClient;

/**************************
 * DECLARATIONS
 *************************/
THSensor *getSensor(String name);
Actuator *getActuator(String name);
void readSensors();
time_t getNtpTime();
bool initTimers();

// www
void handleActuratorChange(AsyncWebServerRequest *request);
void handleActurators(AsyncWebServerRequest *request);
void handleSensordata(AsyncWebServerRequest *request);
void handleSensordataCurrent(AsyncWebServerRequest *request);
void handleSensors(AsyncWebServerRequest *request);
void handleSensorTypes(AsyncWebServerRequest *request);
void handleConfig(AsyncWebServerRequest *request);

void initOTA();
void loadSettings(fs::FS &fs);
void setLEDState(LEDState state);
void updateLEDState();

/**************************
 * DEFINITIONS
 *************************/
void setup()
{

    // start debug output
    Serial.begin(115200);

    // status LED
    statusLED.Begin();
    setLEDState(LEDState::WIFI_STATE_CONNECTING);

    // WiFi and HTTP
    wifiManager.setConnectTimeout(10);
    if (!wifiManager.autoConnect())
    {
        Serial.println("failed to connect, we should reset as see if it connects");
        setLEDState(LEDState::ERROR);
    }

    // setup mDNS
    char hostname[20];
    uint64_t chipid = ESP.getEfuseMac();
    sprintf(hostname, "esp32-%04X%08X", (uint16_t)(chipid >> 32), (uint32_t)chipid);
    if (!MDNS.begin(hostname))
    {
        Serial.println("Error setting up MDNS responder!");
    }
    else
    {
        Serial.println("mDNS responder started");
    }

    // init OTA update
    // @todo: activate only if jumper is set
    initOTA();

    // init File system and show content
    if (!LittleFS.begin(false))
    {
        setLEDState(LEDState::ERROR);
        while (true)
        {
            debug.println("Failed to mount file system");
            delay(1000);
        }
    }
    listDir(LittleFS, "/", 0);

    // settings
    loadSettings(LittleFS);

    // sync time
    setSyncProvider(getNtpTime);

    // init timers
    while (!initTimers())
    {
        delay(100);
    }

    readSensors();

    // HTTP handles
    server.begin();
    server.serveStatic("/", LittleFS, "/www/");

    // API
    server.on("/api/actuators", HTTP_GET, handleActurators);
    server.on("/api/actuator/change", HTTP_POST, handleActuratorChange);
    server.on("/api/sensors/all", HTTP_GET, handleSensordata);
    server.on("/api/sensors/current", HTTP_GET, handleSensordataCurrent);
    server.on("/api/config", handleConfig);
    server.on("/reboot", [](AsyncWebServerRequest *r) { // return current device time
        String time = String(now());
        r->send(200, "text/json", "{\"answer\": \"ok\"}");
        delay(100);
        ESP.restart();
    });
    server.on("/api/time", [](AsyncWebServerRequest *r) { // return current device time
        String time = String(now());
        r->send(200, "text/json", "{\"time\": \"" + time + "\"}");
    });
    server.on("/api/stats", [](AsyncWebServerRequest *r) { // return current device time
        r->send(200, "text/json", "{\"free_heap\": \"" + String(ESP.getFreeHeap()) + "\", "
                                                                                     "\"chip_rev\" : \"" +
                                      ESP.getChipRevision() + "\", "
                                                              "\"sdk\" : \"" +
                                      ESP.getSdkVersion() + "\", "
                                                            "\"wifi\" : \"" +
                                      WiFi.RSSI() + "\", "
                                                    "\"LITTLEFS_used\" : \"" +
                                      LittleFS.usedBytes() + "\", "
                                                             "\"cpu_freq\" : \"" +
                                      ESP.getCpuFreqMHz() + "\"}");
    });

    // init telnetServer
    debug.setTelnet(&telnetServer, &telnetClient);
    telnetServer.begin();
    telnetServer.setNoDelay(true);

    setLEDState(LEDState::NONE);

#ifdef MOCKUP_DATA
    debug.print("Creating mockup data...");
    time_t t = now();
    for (size_t n = 0; n < SENSORS_BUFSIZE; n++)
    {
        buffer_time.add(t++, true);
        for (size_t i = 0; i < sensors.size(); i++)
        {
            THSensor *s = sensors.get(i);
            if (s->isEnabled())
            {
                sensors.get(i)->updateTH();
                digitalWrite(LED_BUILTIN, !digitalRead(LED_BUILTIN));
            }
        }
    }
    debug.println("done!");
#endif
}

void loop()
{
    // check WiFi an reconnect if necessary
    if (WiFi.status() != WL_CONNECTED)
    {
        debug.println(WiFi.status());
        setLEDState(LEDState::WIFI_STATE_DISCONNECTED);
        wifiManager.autoConnect();
    }

    // handle OTA updates
    ArduinoOTA.handle();

    // sync time
    if (timeStatus() == timeNotSet)
    {
        debug.println("Waiting for synced time");
    }

    // add new telnet Clients
    if (telnetServer.hasClient())
    {
        if (!telnetClient || !telnetClient.connected())
        {
            if (telnetClient)
            {
                telnetClient.stop();
                debug.println("Telnet Client Stop");
            }
            telnetClient = telnetServer.accept();
            debug.println("New Telnet client");
            telnetClient.clear();
            telnetClient.println("Welcome to TerraESP");

            // print config
            File dataFile = LittleFS.open("/config.json", FILE_READ);
            String json = dataFile.readString();
            dataFile.close();
            debug.println(json);

            // print NTP
            getNtpTime();
        }
    }

    // read current sensor values
    auto current = millis();
    if ((current - last_sensors) / 1000. >= SENSORS_PAUSE_S)
    {
        readSensors();
        last_sensors = current;
        debug.printf("Free heap %d min free heap %d stack %d\n", ESP.getFreeHeap(), ESP.getMinFreeHeap(), uxTaskGetStackHighWaterMark(NULL));
    }

    // update thresholds -> deactivates thresholds after duration
    for (size_t i = 0; i < thresholds.size(); i++)
    {
        thresholds[i]->update();
    }

    // delay, handle alarms/sensors and so on
    // Alarm.delay(10);

    // handle timers
    struct tm timeinfo;
    if (getLocalTime(&timeinfo))
    {
        for (size_t i = 0; i < timers.size(); i++)
        {
            timers[i]->update(timeinfo);
        }
    }
    else
    {
        debug.println("Failed to obtain time");
    }

    delay(100);
}

/**
 * @brief load settings an initialize sensors, buttons, timers, thresholds, ...
 *
 * @param fs FileSystem
 */
void loadSettings(fs::FS &fs)
{
    File dataFile = fs.open("/config.json", FILE_READ);
    String json = dataFile.readString();
    dataFile.close();
    debug.println(json);
    JsonDocument doc;
    DeserializationError error = deserializeJson(doc, json);
    if (error)
    {
        debug.println("----- parseObject() for config.json failed -----");
        debug.println(error.c_str());
        return;
    }
    else
    {
        // load sensor settings
        JsonArray sensorsJSON = doc["sensors"];
        for (auto s : sensorsJSON)
        {
            debug.print("Got new sensor ");
            debug.print(s["type"].as<String>());
            debug.print(" on pin/address ");
            debug.print(s["gpio"].as<String>());
            debug.println();
            String type((const char *)s["type"]);
            type.toLowerCase();
            THSensor *thsensor = nullptr;
            if (type.startsWith("dht") || type.startsWith("am23"))
            {
                // DHTType dht_type = DHTType::UNKNOWN;
                uint8_t dht_type = 0;
                if (type == "dht22" || type == "am2302" || type == "am2321")
                {
                    dht_type = DHT22;
                }
                else if (type == "dht11")
                {
                    dht_type = DHT11;
                }
                else if (type == "dht21" || type == "am2301")
                {
                    dht_type = DHT21;
                }
                // if (type == "dht22")
                // {
                //     dht_type = DHTType::DHT22;
                // }
                // else if (type == "am2302")
                // {
                //     dht_type = DHTType::AM2302;
                // }
                // else if (type == "dht21")
                // {
                //     dht_type = DHTType::DHT21;
                // }
                // else if (type == "dht11")
                // {
                //     dht_type = DHTType::DHT11;
                // }
                // else if (type == "dht2301")
                // {
                //     dht_type = DHTType::AM2301;
                // }
                // if (dht_type != DHTType::UNKNOWN)
                // {
                //     thsensor = new DHT11Sensor(s["name"], s["gpio"], dht_type);
                // }
                if (dht_type != 0)
                {
                    thsensor = new DHT11Sensor(s["name"], s["gpio"], dht_type);
                }
            }
            else if (type == "sht31")
            {
                thsensor = new SHT31Sensor(s["name"], s["gpio"]);
            }
            else if (type == "ds18b20")
            {
                thsensor = new DS18B20Sensor(s["name"], s["gpio"], s["idx"].is<JsonVariant>() ? s["idx"] : 0);
            }
            else if (type == "analog_t")
            {
                thsensor = new AnalogSensor(s["name"], s["gpio"], true, false);
            }
            else if (type == "analog_h")
            {
                thsensor = new AnalogSensor(s["name"], s["gpio"], false, true);
            }
            else
            {
                debug.println(" unknown");
            }

            if (thsensor)
            {
                if (!s["enabled"].isNull())
                {
                    thsensor->setEnabled(s["enabled"]);
                }
                sensors.push_back(thsensor);
            }
        }

        // load actuators
        JsonArray actuatorsJSON = doc["actuators"];
        for (auto a : actuatorsJSON)
        {
            String name = a["name"];
            uint16_t gpio = (uint16_t)a["gpio"];
            bool inverted = a["inverted"];
            uint16_t minVal = a["min"];
            uint16_t maxVal = a["max"];

            if (strcmp(a["type"], "toggle") == 0)
            {
                actuators.push_back((Actuator *)new ActuatorToggle(name, gpio, inverted));
            }
            else
            {
                actuators.push_back((Actuator *)new ActuatorPWM(name, gpio, minVal, maxVal));
            }
            debug.println("Got new " + actuators[actuators.size() - 1]->toString());
        }

        // load timer settings
        JsonArray timerJSON = doc["timers"];
        for (auto t : timerJSON)
        {
            Actuator *actuator = getActuator(t["actuator"].as<String>());
            if (actuator)
            {
                Timer *timer = new Timer(t["name"].as<String>(),
                                         actuator,
                                         split(String((const char *)t["on"]), ':', 0).toInt(),
                                         split(String((const char *)t["on"]), ':', 1).toInt(),
                                         split(String((const char *)t["off"]), ':', 0).toInt(),
                                         split(String((const char *)t["off"]), ':', 1).toInt());
                timer->setEventList(&events);
                timer->setDebug(debug);
                timers.push_back(timer);
            }
        };

        // load thresholds
        JsonArray thresholdsJSON = doc["thresholds"];
        for (auto s : thresholdsJSON)
        {
            THSensor *sensor = getSensor(s["sensor"].as<String>());
            Actuator *actuator = getActuator(s["actuator"].as<String>());
            // if sensor and actuator exist create threshold
            if (sensor && actuator)
            {
                Threshold::SensorType sensor_type = Threshold::SensorType::UNKNOWN;
                if (s["sensor_type"].as<String>() == "humidity")
                {
                    sensor_type = Threshold::SensorType::HUMIDITY;
                }
                else if (s["sensor_type"].as<String>() == "temperature")
                {
                    sensor_type = Threshold::SensorType::TEMPERATURE;
                }
                else
                {
                    debug.printf("Threshold %s sensor type %s is unknown\n", s["name"].as<String>().c_str(), s["sensor_type"].as<String>().c_str());
                }

                bool greater_than = false;
                if (s["comparator"].as<String>() == ">")
                {
                    greater_than = true;
                }

                Threshold *thresh = new Threshold(s["name"].as<String>(),
                                                  sensor,
                                                  actuator,
                                                  s["duration"],
                                                  s["threshold"],
                                                  greater_than,
                                                  s["inverted"],
                                                  s["gap"],
                                                  sensor_type);
                thresh->setEventList(&events);
                thresholds.push_back(thresh);
            }
        }

        // general settings
        JsonObject generalJSON = doc["general"];
        settings_time.dst = (bool)generalJSON["dst"];              // daylight saving time
        settings_time.gmt_offset = (int)generalJSON["gmt_offset"]; // gmt offset
    }
}

/**************************************
 *
 * OTA Update
 *
 *************************************/

/**
 * @brief Inits the OTA Update
 *
 */
void initOTA()
{
    // Port defaults to 3232
    // ArduinoOTA.setPort(3232);

    // Hostname defaults to esp3232-[MAC]
    ArduinoOTA.setHostname(host.c_str());

    // Password can be set with it's md5 value as well
    // MD5(admin) = 21232f297a57a5a743894a0e4a801fc3
    ArduinoOTA.setPasswordHash("21232f297a57a5a743894a0e4a801fc3");

    ArduinoOTA.onStart([]()
                       {
        String type;
        if (ArduinoOTA.getCommand() == U_FLASH)
        {
            type = "sketch";
        }
        else
        {
            // U_LITTLEFS
            type = "filesystem";
        }

        // NOTE: if updating LITTLEFS this would be the place to unmount LITTLEFS using LITTLEFS.end()
        debug.println("Start updating " + type); });
    ArduinoOTA.onEnd([]()
                     {
        debug.println("\nEnd");
        ESP.restart(); });
    ArduinoOTA.onProgress([](unsigned int progress, unsigned int total)
                          {
        // setLEDState(LEDState::OTA_ACTIVE);
        RgbColor updatedColor = RgbColor::LinearBlend(RgbColor(50, 0, 0), RgbColor(0, 50, 0), (progress / (float)total));
        statusLED.SetPixelColor(0, updatedColor);
        statusLED.Show();
        debug.printf("Progress: %u%%\r", (progress / (total / 100))); });
    ArduinoOTA.onError([](ota_error_t error)
                       {
        debug.printf("Error[%u]: ", error);
        setLEDState(LEDState::ERROR);
        if (error == OTA_AUTH_ERROR)
            debug.println("Auth Failed");
        else if (error == OTA_BEGIN_ERROR)
            debug.println("Begin Failed");
        else if (error == OTA_CONNECT_ERROR)
            debug.println("Connect Failed");
        else if (error == OTA_RECEIVE_ERROR)
            debug.println("Receive Failed");
        else if (error == OTA_END_ERROR)
            debug.println("End Failed"); });
    ArduinoOTA.begin();
    debug.println("OTA update ready");
}

/**************************************
 *
 * HTTP handler
 *
 *************************************/
/**
 * @brief Checks if path exists
 *
 * @param path URL
 * @return true exists
 * @return false does not exist
 */
bool exists(String path)
{
    bool exists = false;
    File file = LittleFS.open(path, FILE_READ);
    if (!file.isDirectory())
    {
        exists = true;
    }
    file.close();
    return exists;
}

/**
 * @brief Sends buffered timestamps and sensor value for all sensors as JSON object for charts, ...
 *
 */
void handleSensordata(AsyncWebServerRequest *request)
{
    JsonDocument doc;
    JsonArray sensor_array = doc["sensors"].to<JsonArray>();
    JsonArray thresholds_array = doc["thresholds"].to<JsonArray>();
    JsonArray events_array = doc["events"].to<JsonArray>();
    JsonArray time_array = doc["time"].to<JsonArray>();

    for (size_t i = 0; i < buffer_time.numElements(); i++)
    {
        time_array.add(*buffer_time.peek(i));
    }
    for (size_t i = 0; i < sensors.size(); i++)
    {
        THSensor *s = sensors[i];
        if (s->isEnabled())
        {
            JsonObject sensor = sensor_array.add<JsonObject>();
            sensor["name"] = s->getName();
            if (s->hasTemperature())
            {
                JsonArray t = sensor["temperature"].to<JsonArray>();
                for (size_t j = 0; j < s->buffer_t.numElements(); j++)
                {
                    t.add(*s->buffer_t.peek(j));
                }
            }
            if (s->hasHumidity())
            {
                JsonArray h = sensor["humidity"].to<JsonArray>();
                for (size_t j = 0; j < s->buffer_h.numElements(); j++)
                {
                    h.add(*s->buffer_h.peek(j));
                }
            }
        }
    }
    for (size_t i = 0; i < thresholds.size(); i++)
    {
        Threshold *thresh = thresholds[i];
        JsonObject t = thresholds_array.add<JsonObject>();
        t["name"] = thresh->getName();
        t["threshold"] = thresh->getThreshold();
        t["greater_than"] = thresh->isGreaterThan();
    }
    for (size_t i = 0; i < events.numElements(); i++)
    {
        Event *event = events.peek(i);
        JsonObject e = events_array.add<JsonObject>();
        e["time"] = event->getTime();
        e["type"] = event->getType();
        e["name"] = event->getEventString();
        e["description"] = event->getDescription();
    }

    debug.printf("Free heap %d min free heap %d stack %d\n", ESP.getFreeHeap(), ESP.getMinFreeHeap(), uxTaskGetStackHighWaterMark(NULL));
    debug.printf("JSON doc size overflowed: %d\n", doc.overflowed());
    debug.flush();

    // send JSON response
    AsyncResponseStream *response = request->beginResponseStream("application/json");
    // serializeJson(doc, debug);
    serializeJson(doc, *response);
    request->send(response);
}

void handleSensordataCurrent(AsyncWebServerRequest *request)
{
    JsonDocument doc;
    JsonArray sensor_array = doc["sensors"].to<JsonArray>();

    for (size_t i = 0; i < sensors.size(); i++)
    {
        THSensor *s = sensors[i];
        if (s->isEnabled())
        {
            JsonObject sensor = doc.add<JsonObject>();
            sensor["name"] = s->getName();
            if (s->hasTemperature())
            {
                sensor["temperature"] = s->readTemperature();
            }
            if (s->hasHumidity())
            {
                sensor["humidity"] = s->readHumidity();
            }
        }
    }

    // send JSON response
    AsyncResponseStream *response = request->beginResponseStream("application/json");
    // serializeJson(doc, debug);
    serializeJson(doc, *response);
    request->send(response);
}
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

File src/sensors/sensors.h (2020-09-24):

#ifndef SENSORS_H
#define SENSORS_H

#include <Arduino.h>
#include <RingBufCPP.h>

#define SENSORS_BUFSIZE 288

class THSensor
{
public:
    THSensor();
    THSensor(String name);
    ~THSensor();

    virtual float readTemperature() = 0;
    virtual float readHumidity() = 0;
    float readLastTemperature();
    float readLastHumidity();
    virtual bool hasTemperature() = 0;
    virtual bool hasHumidity() = 0;
    bool updateTH();
    virtual bool running() = 0;

    String getName();
    void setEnabled(bool enabled);
    bool isEnabled();

    RingBufCPP<float, SENSORS_BUFSIZE> buffer_h;
    RingBufCPP<float, SENSORS_BUFSIZE> buffer_t;

    enum class SENSOR_TYPE
    {
        UNKNOWN,
        DHT,
        SHT31,
        ANALOG_TEMPERATURE,
        ANALOG_HUMIDITY,
        ANALOG_TEMPERATURE_K,
        DS18B20
        // change last value in stringToSensor and getSensorTypes if you add an additional sensor
    };

#define SENSOR_TYPE_SIZE 7

    static String sensorToString(SENSOR_TYPE t)
    {
        switch (t)
        {
        case SENSOR_TYPE::DHT:
            return "DHT";
        case SENSOR_TYPE::SHT31:
            return "SHT31";
        case SENSOR_TYPE::ANALOG_TEMPERATURE:
            return "analog_t";
        case SENSOR_TYPE::ANALOG_HUMIDITY:
            return "analog_h";
        case SENSOR_TYPE::ANALOG_TEMPERATURE_K:
            return "analog_t_k";
        case SENSOR_TYPE::DS18B20:
            return "DS18B20";
        case SENSOR_TYPE::UNKNOWN:
            break;
        }
        return "unknown";
    }

    static SENSOR_TYPE stringToSensor(String s)
    {
        int num_sensor_types = ((int)SENSOR_TYPE::DS18B20 + 1);
        // iterate over sensors and return type if name equal
        for (int i = (int)SENSOR_TYPE::UNKNOWN; i < num_sensor_types; i++)
        {
            SENSOR_TYPE type = static_cast<SENSOR_TYPE>(i);
            if (s.equals(sensorToString(type)) == 0)
            {
                return type;
            }
        }
        return SENSOR_TYPE::UNKNOWN;
    }

protected:
    String m_name = "null";
    bool m_running = false;
    bool m_enabled = true;
};

#endif

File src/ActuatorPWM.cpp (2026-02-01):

#include "ActuatorPWM.h"

ActuatorPWM::ActuatorPWM(String name, uint8_t gpio, uint16_t minVal, uint16_t maxVal) : Actuator(name, gpio), minVal(minVal), maxVal(maxVal)
{
    initGPIO();
}

ActuatorPWM::~ActuatorPWM()
{
}


uint16_t ActuatorPWM::getMin()
{
    return minVal;
}

uint16_t ActuatorPWM::getMax()
{
    return maxVal;
}

uint16_t ActuatorPWM::getValue()
{
    return ledcRead(gpio);
}

void ActuatorPWM::setValue(uint16_t value)
{
    // if (value == LOW && initialized)
    // {
    //     turnOff();
    // }
    // else
    // {
    //     if (!initialized)
    //     {
    //         initGPIO();
    //     }
        if (value == HIGH)
            value = maxVal;
        value = min(value, maxVal);
        debug.printf("Change PWM on GPIO %d to value: %d\n", gpio, value);
        ledcWrite(gpio, value);
    // }
}

void ActuatorPWM::turnOn()
{
    debug.printf("Change PWM on GPIO %d to value: %d\n", gpio, maxVal);
    ledcWrite(gpio, maxVal);
}

void ActuatorPWM::turnOff()
{
    debug.printf("Turn off PWM on GPIO %d\n", gpio);
    deinitGPIO();
    pinMode(gpio, OUTPUT);
    digitalWrite(gpio, LOW);
}

void ActuatorPWM::initGPIO()
{
    ledcAttach(gpio, 24000, 10);  // 24 kHz, 10 bit
    initialized = true;
}

void ActuatorPWM::deinitGPIO()
{
    ledcDetach(gpio);
    initialized = false;
}

String ActuatorPWM::toString()
{
    return "ActuatorPWM " + name + " GPIO=" + String(gpio) +
           " min=" + String(minVal) + " max=" + String(maxVal);
}

ActuatorType ActuatorPWM::getType(){
    return ActuatorType::ACTUATOR_SLIDER;
}

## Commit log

2018-01-03 Added OTA update Device creates Access Point if WiFi network is not reachable (for first config) Fixed some time sync issues Added multiple retries for DHT sensor readout (there are many communicatio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
2018-01-08 Added Serial/Telnet debug output Modified upload.sh - doesn't overwrite config.json on device js librarys are stored local on the device (so internet access is only needed for time update) Some minor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
2019-09-10 Added new sensors
2019-09-16 Different sensors are working now Reading sensors from config file
2019-09-16 Added prototype PCB layout
    [pcb2.fzz]
2019-10-05 Updated to ArduinoJSON6 Updated Webinterface Compressed CSS/JS files
    [pcb.fzz, pcb0_2.fzz]
2019-10-06 Added new classes for Threshold and Timer buttons, sensors, timers, thresholds should work now
2019-10-08 Added events (button toggle, timer, threshold reached) Bugfixes
    [Threshold.cpp, Timer.cpp, terraesp.cpp]
2019-11-07 New sensors Switched to AngularJS SPA (in progress...)
2020-12-06 - Many bugfixes - Webinterface is working - create_www.sh bundles all dependencies in one lib (webinterface loads much faster, no exceptions because of too many parallel streams anymore)
    [terraesp.cpp]
2021-01-18 Bugfixes for analog sensor and PWM actuator
    [terraesp.cpp]
2021-01-30 Switched from chart.js to flot.js Several bugfixes Removed TimeAlarms lib and made own timer Added bootstrap toggle for webinterface
2021-01-30 Several bugfixes Removed TimeAlarms lib and made own timer Added bootstrap toggle for webinterface
    [Threshold.cpp, Timer.cpp, terraesp.cpp]
2021-01-30 Updated README.md Deleted old Fritzing PCB Converted EAGLE project to KiCAD (not tested yet!)
    [pcb.fzz, pcb0_2.fzz, pcb0_3.fzz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]
2021-02-20 Updated README Created KiCAD PCB (in progress)
    [ssr.sch, terraesp2.kicad_pcb, terraesp2.sch]
2021-02-21 Fixed Time.h conflict on Windows
    [terraesp.cpp]
2021-03-27 Switched back to Adafruit lib for DHT sensors
2021-12-21 removed old DHT sensor lib
2023-10-24 Updated platformio.ini and fixes #6
    [Threshold.cpp, terraesp.cpp]
2026-02-12 Updated to latest ArduinoJson 7
2026-02-12 Fixed threshold bug that immediately deactivates turned on actuators
    [Threshold.cpp]

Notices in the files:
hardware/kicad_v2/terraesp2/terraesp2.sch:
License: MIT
